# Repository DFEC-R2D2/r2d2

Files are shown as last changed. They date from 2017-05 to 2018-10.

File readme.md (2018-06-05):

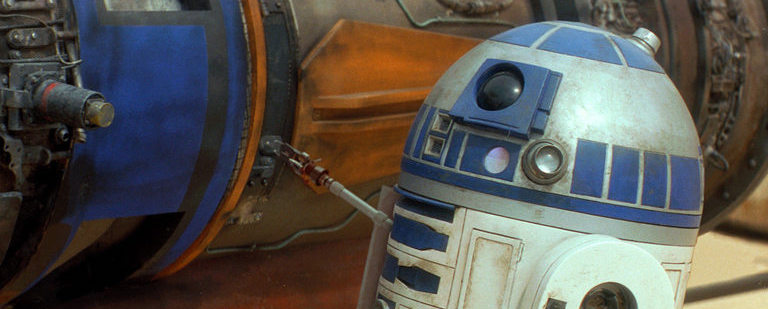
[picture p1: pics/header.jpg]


# R2-D2 Senior Design Project

This repo documents the progress of the R2-D2 design for the 2017-2018 class year. R2-D2's purpose, once
it is delivered, is to:

- Serve as an example of multi-disciplinary engineering
- Support internal events like: Major's Night, DF events, and DFEC events
- Support external events like: STEM outreach and recruiting events.

# Team

- C1C Anthony Talosaga: power system and software
- C1C Hwi Tae Kim: software
- C1C Brayden Thomas: mechanical design and overall build
- C1C Mario Bracamonte: mechanical design and electrical PCD design/construction

# Architecture

## Power

The power system is modeled around a common 12V system. Relays are used to route power for emergency stop, charging, or other reasons. The 12V is split into 5V and 3.3V using voltage regulators to power the raspberry pi, Arduino, pololu motor driver, LED matrix, servos, fan, and the sabertooth motor driver.

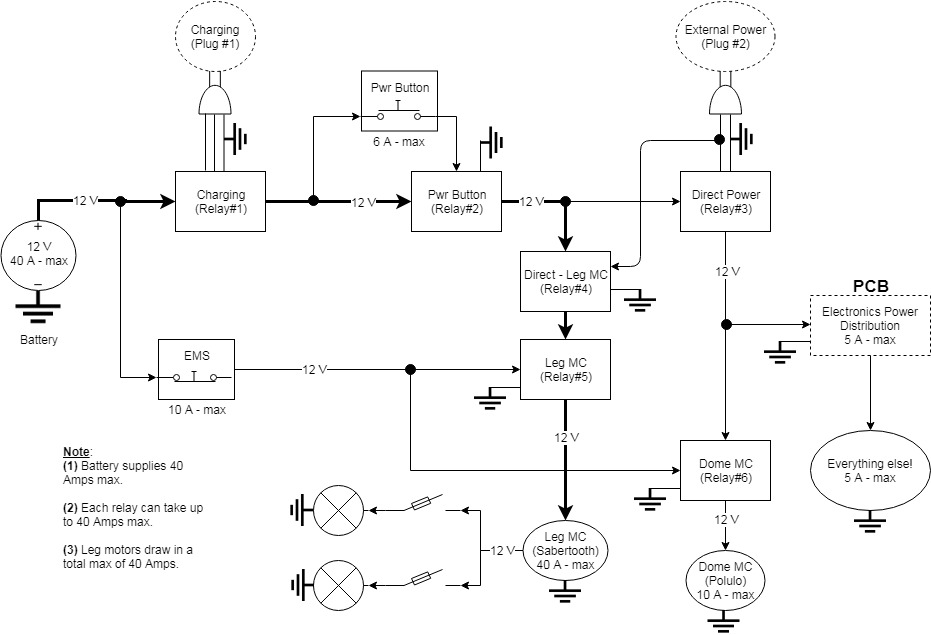
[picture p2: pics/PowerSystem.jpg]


The type of battery that we used for R2D2 is the Motorcycle Battery called Battery Tender Lithium Battery from Deltran. This battery is made from Lithium Iron Phosphate and supplies 12V with 26-35 Amps of power. This allows us to power all the components in R2D2 as well as providing power to the motors, which take up majority of the current.

## Data

The system data shows the wiring between the pi and all of the sensors and effectors. Most of the communications operates at 3.3v, however, there is a USB serial that operates at 5v (5V TTL). The pi uses all of the buses available to it: I2C at 100 Hz, SPI, and USB. The PWM to drive the servos is off loaded to a hardware servo controller board. Similarly, the PWM which drives the motors is offloaded to 2 different motor controllers (Sabertooth and SMC).

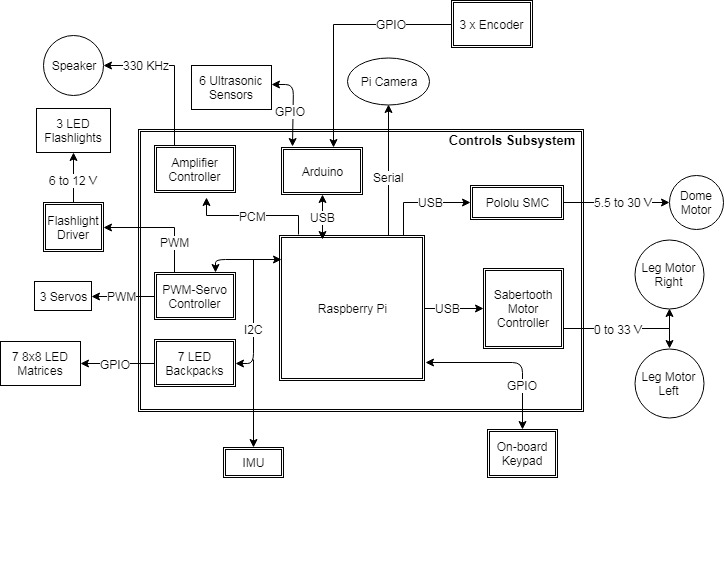
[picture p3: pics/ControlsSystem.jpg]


## Software Operating Modes

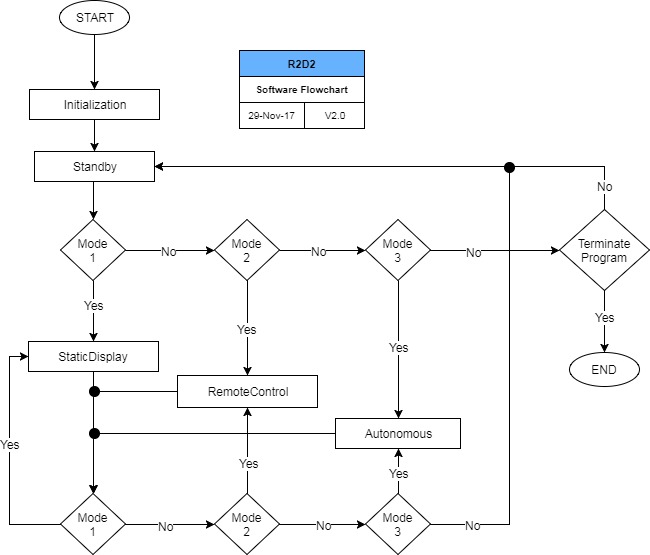
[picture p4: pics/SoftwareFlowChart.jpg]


The system shall follow the transition diagram shown above with the following definitions:

- **Off:** The off mode of R2D2 is when R2D2 is powered off or without any power source. This means that none of the operations are possible, and R2D2 non-functional.
- **Standby:** The standby mode of R2D2 is when R2D2 is remaining idle. None of the motors or the sensors are working in this mode. The Standby mode operates to allow users the ability to fix problems. It is the default mode upon turning R2D2 on.
- **Remote Controlled:** The remote mode of R2D2 can be controlled through the PS4 controller. The instructions on how to connect the PS4 controller to R2D2 can be found in the operational manual. All functionalities of R2D2 is present in this mode.
- **Static Display:** The display mode of R2D2 is used to showcase R2D2. This means that R2D2 is not capable of moving, because it is in display mode. The display mode will respond to people that are close to R2D2.

# Software

R2 is written primarily in python. The following libraries were developed for R2-D2:

- [Text-to-Astromech: ttastromech](https://pypi.python.org/pypi/ttastromech)
- [Simple Motor Controler: smc](https://pypi.python.org/pypi/smc)
- [Sabertooth Motor Controller: pysabertooth](https://pypi.python.org/pypi/pysabertooth)

The following are used:

- [mote](https://github.com/MomsFriendlyRobotCompany/mote)
- [fake_rpi](https://pypi.python.org/pypi/fake-rpi)
- [opencvutils](https://pypi.python.org/pypi/opencvutils)
- [nxp_imu](https://pypi.python.org/pypi/nxp-imu)

Folder structure

```bash
r2d2
|- final_design
   |- arduino
   |- mechanical
   |- node
   |   |-nodejs
   |     |- scripts
   |     |- movies
   |     |- pics
   |- python
      |- clips
      |- library
      |- states
```

- `arduino`: contains the Arduino code. The Arduino talks to the ultrasound sensors and measures the battery voltage
- `mechanical`: containes STL files of parts designed for R2
- `node`: R2's webpage is programmed using nodejs. The `script` folder contains 2 scripts to: 
    - `build_webpages.sh`: generate the webpage html files from Markdown and installs them in the correct location.
    - `gen_qr_code.py`: generate a QR code to enable people to easily access R2's webpage.
- `python`: this is the main *robot* code for R2. The main program is `run.py`.
    - `clips.json`: is a list of available Star Wars sound clips R2 can play

Currently, the Raspberry Pi 3 image that we created allows R2D2 to automatically run this code when booted on. All the USB devices that are connected to the R2D2 are based on our actual model, and would need to be changed to match the serial information of the new device if you are considering making another R2D2. If needed, the image file can be acquired through the DFEC Department Instructor Major Kevin Walchko.

R2 has 3 primary states:

- **standby():** This function is the standby mode function and the default state of R2. Standby does nothing but *standby* for something to happen. If there is an error during operation, R2 switches from his current operating mode and falls into standby. Since standby does nothing, it is seen as the safest mode.
- **static():** This function is the static mode. Static mode is the display mode and it is designed not to allow the leg motors to move. Infact, the electrical design flips a relay and cuts off leg motor power in this state. Only the dome motor and the servos are allowed to move in this state.
- **remote():** This function is the remote mode function, it receives the `remoteflag`, which is set by the keypad on R2D2. This flag is set when 3 is pressed, and continues to be set until R2D2 is put into another mode. The remote mode ensure that R2D2 has full capabilities, such that the motor control works, and all its functionalities are present. R2D2 will be controlled through the PS4 controller. The instructions for connecting the PS4 controller to R2D2 can be found in the operations manual.

| State | Dome Motor | Leg Motors | Audio | Camera | LEDS/Lights | Servos |
|---|---|---|---|---|---|---|
| Standby | | | X | | X | |  
| Remote  | X | X | X | | X | X | 
| Static  | X | | X | X | X | X | 

Helper functions:

- **reboot():** This function is the reboot function. 
- **shutdown():** This function is the shutdown function. 

R2 has to have some personnality, so he is setup with these *emotions*:

- **happy():** This function does not have any inputs or outputs, as the commands are given from the function. The happy function turns on the green LED on the 8x8 matrix LED pads, and also spins the dome. The top hatch of R2D2 will open in a wave and close in a wave. This can be either called from the keypad button 4, or from the arrow hat on the controller.
- **confused():** This function does not have any inputs or outputs, as the commands are given from the function. The happy function turns on the orange LED on the 8x8 matrix LED pads. This can be either called from the keypad button 5, or from the arrow hat on the controller.
- **angry():** This function does not have any inputs or outputs, as the commands are given from the function. The happy function turns on the red LED on the 8x8 matrix LED pads, and plays the imperial theme sound. Once the theme sound is complete, it opens the top hatch of R2D2 and closes it afterwards. This can be either called from the keypad button 6, or from the arrow hat on the controller.

# Project in Pictures

The development of R2 followed a standard Aerospace process of building/testing a breadboard, brassboard, and final design. These follow the ideas of form, fit, and function.

- **Breadboard**: This was the first incarnation of R2. As seen below, it consisted of HW/SW that allowed the team to design/test the functional aspects of R2. The breadboard contained either the actual HW R2 would use or surrogate hardware that was in some way representative (as best as we knew it at the time of the build) of the final design.
- **Brassboard**: This was the second incarnation of R2. Building upon the breadboard HW/SW, all surrogate items were swapped out for the correct items. For example, the breadboard had 3 small 12V motors which represented the dome and leg motors. Now in the brassboard, these small motors were replaced with the final R2 motors. The brassboard now allowed us to test both function and fit. Fit refers to the interfaces, both HW and SW. 
- **Final Design**: Usually you would go to a prototype in the Aerospace world, but here we went straight to the final design. This final design now allowed us to test HW/SW form, fit, and function.  Form refers to either the physical dimension (e.g., the size of a box) or a SW size/processing standpoint for our storage system/CPU.

## Functional Development: Breadboard

This was R2's electronics on a box. It allowed full software design/testing with similar hardware without worrying about actually having R2's body built. Although this looks nothing like an R2 unit, it allowed the team to develop a decent first version of R2. Basic functionallity was achieved including:

- Face detection using OpenCV and the PiCamera
- PS4 controller integration, with analog sticks driving motors, buttons moving servos and making R2 sounds

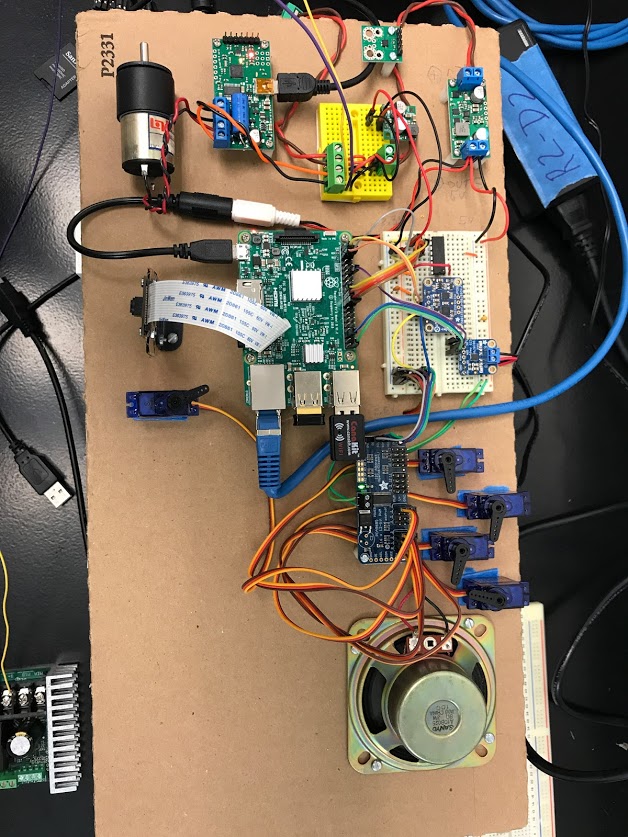
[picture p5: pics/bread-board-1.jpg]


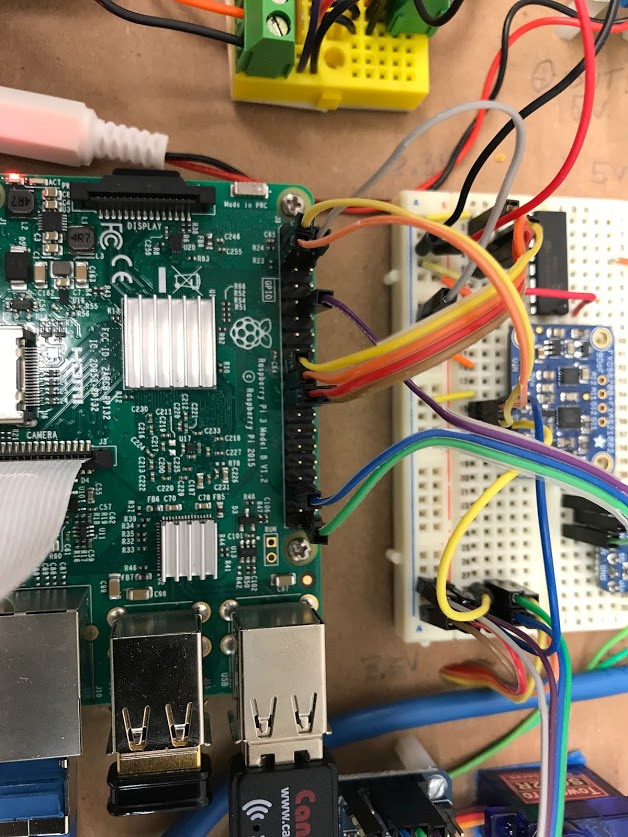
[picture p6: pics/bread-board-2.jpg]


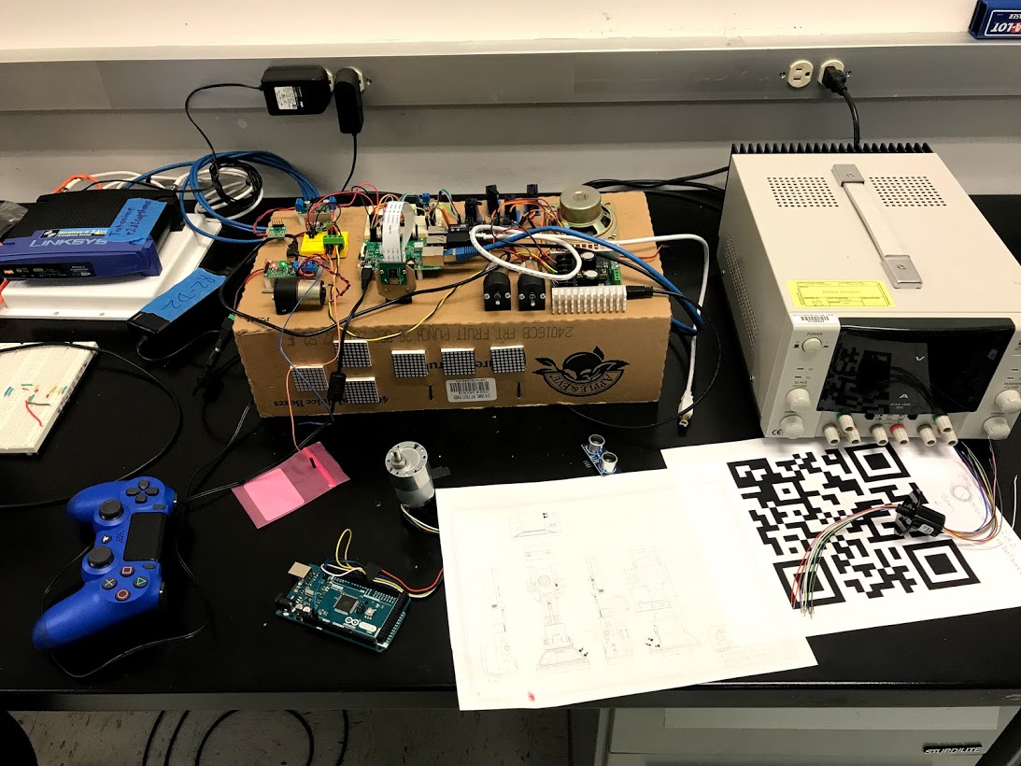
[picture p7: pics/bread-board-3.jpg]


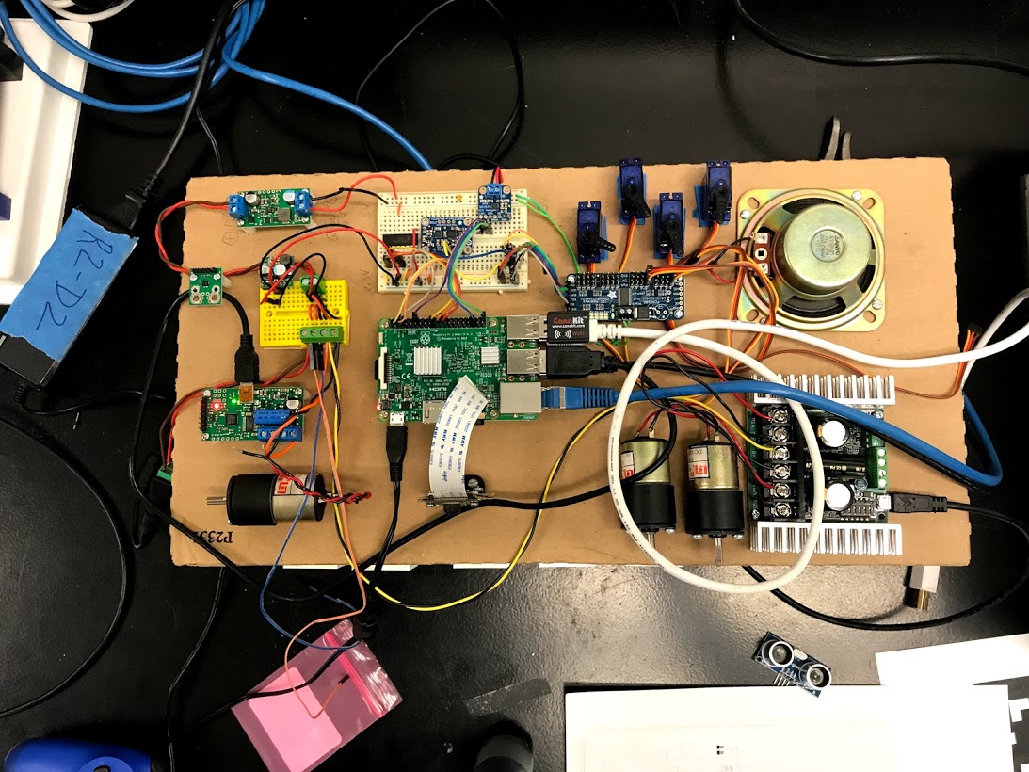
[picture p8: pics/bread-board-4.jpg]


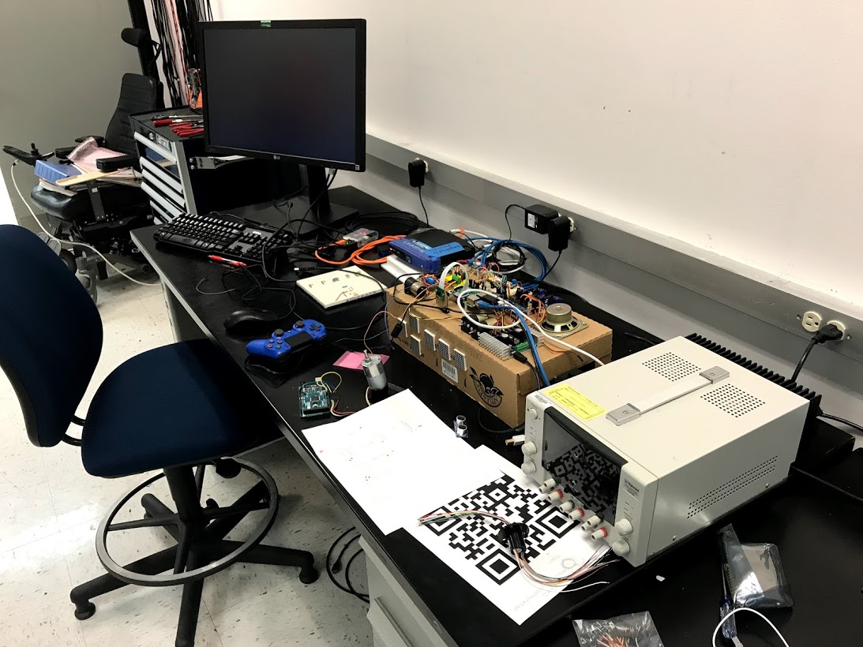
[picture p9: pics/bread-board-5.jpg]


# Fit Development: Brassboard

This was the next level and allowed development/testing against the exact hardware and interfaces in R2. This allowed the team setup the full wiring harness with relays, test out PCBs designed (there were several versions), test out the dome slip ring wiring harness and ensure full HW and SW integration.

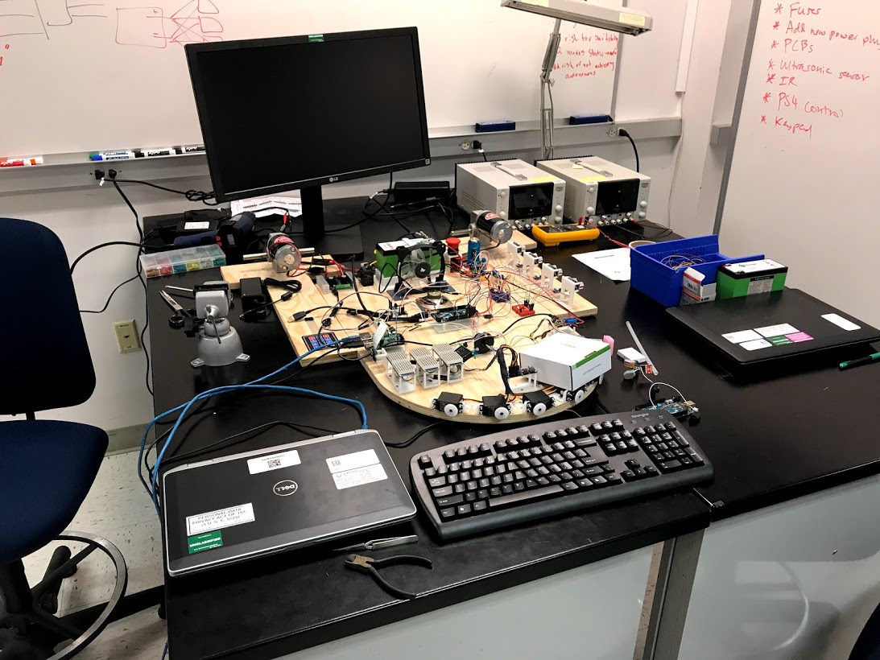
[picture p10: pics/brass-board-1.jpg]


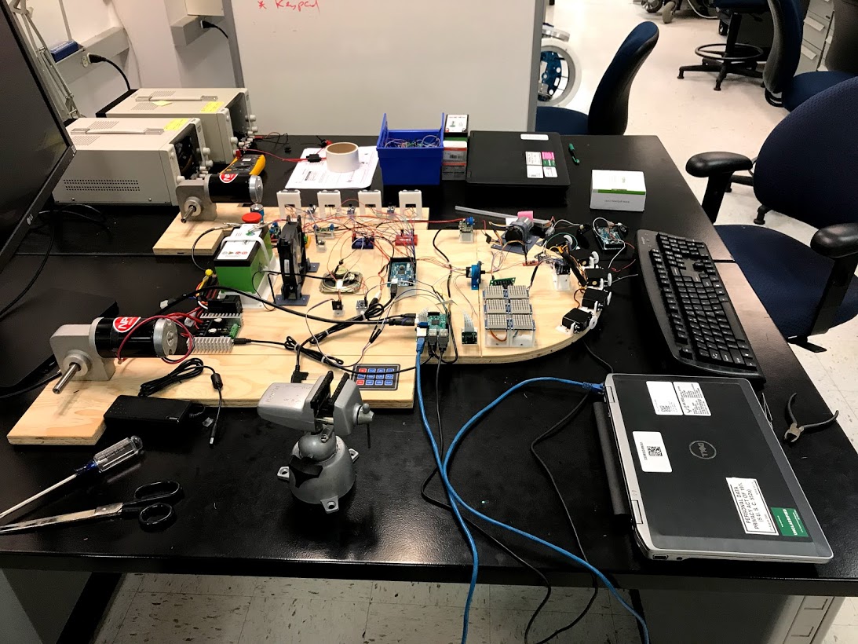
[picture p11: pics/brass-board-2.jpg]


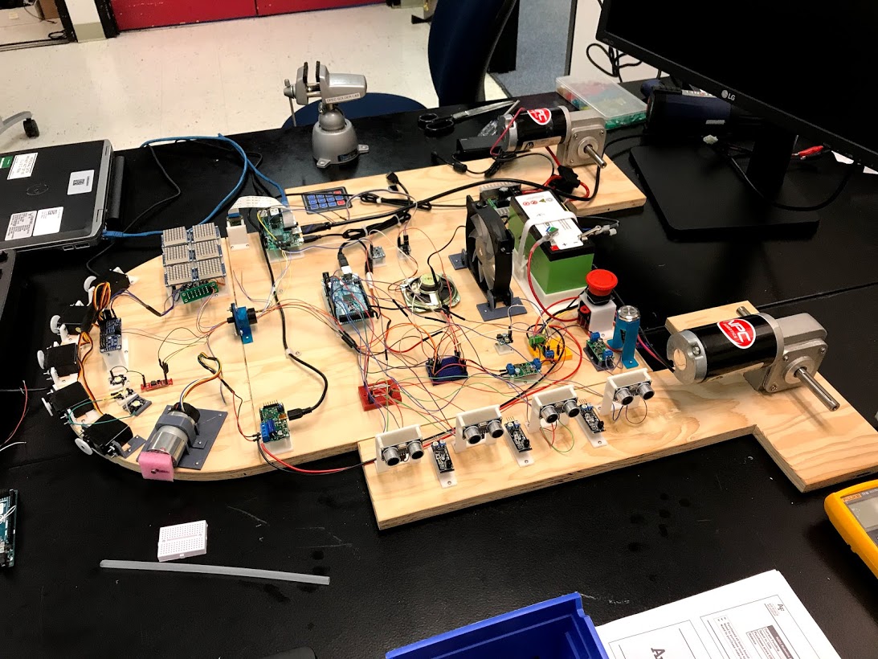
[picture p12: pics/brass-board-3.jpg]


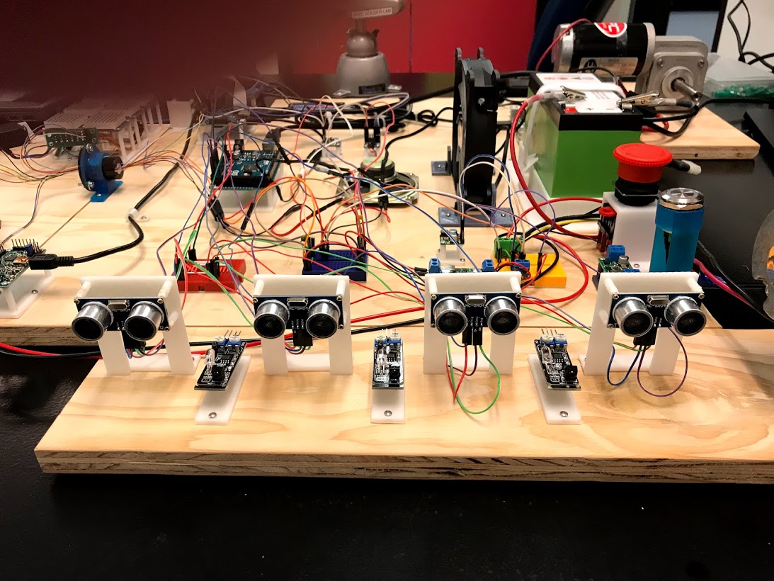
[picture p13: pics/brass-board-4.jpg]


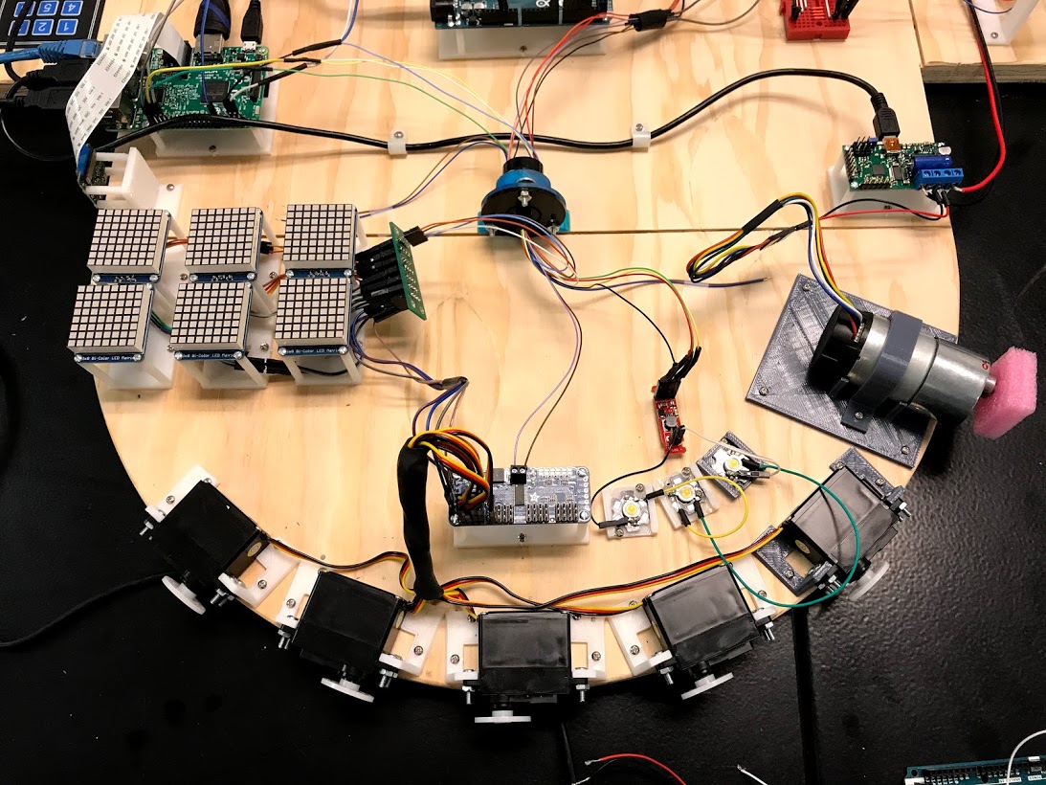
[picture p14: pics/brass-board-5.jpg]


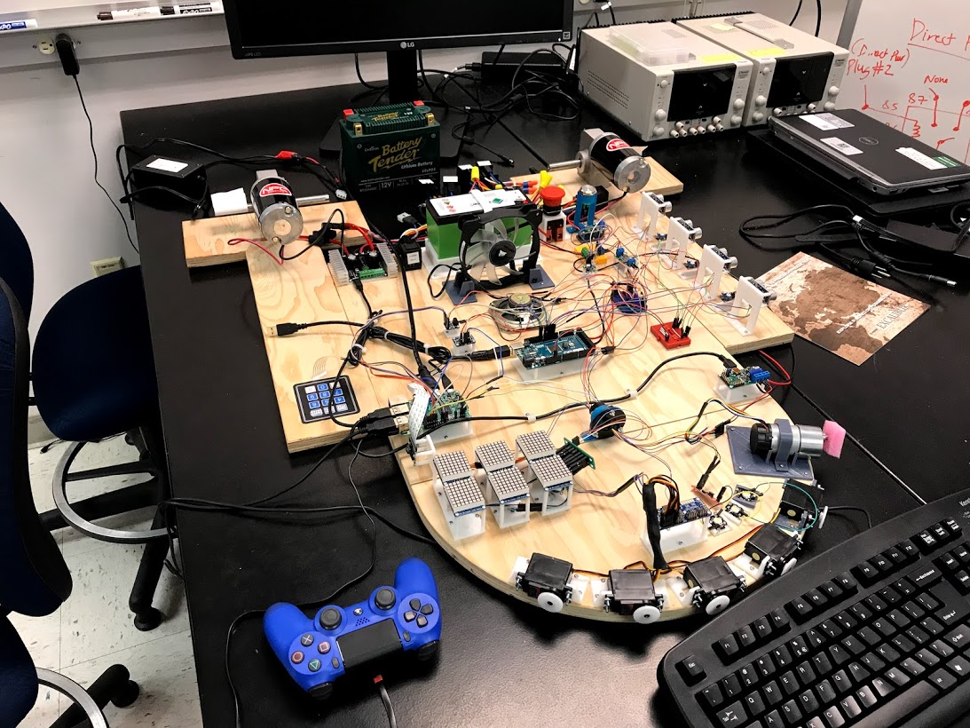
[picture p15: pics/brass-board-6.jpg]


# Final Design and Building

Everything from the brassboard was duplicated and built into the R2. The brassboard was **not** dismantled, but left intact for debugging. The team needed a setup that we could fall back on if HW/SW problems were encountered in the final build. 

Many of the hindges, mounting brackets, etc were designed and 3d printed. The largest design was the 2 rear feet. They were completely designed and 3d printed. Then the motors, wheels, etc were mounted inside and they were painted using Rust-Oleum paint and primer. Unfortunately there were numerous little errors that weren't discovered until everyting was assembled and we had to redesign and rebuild the feet. The feet also took about 2-3 days to print just one ... it was a very slow process.

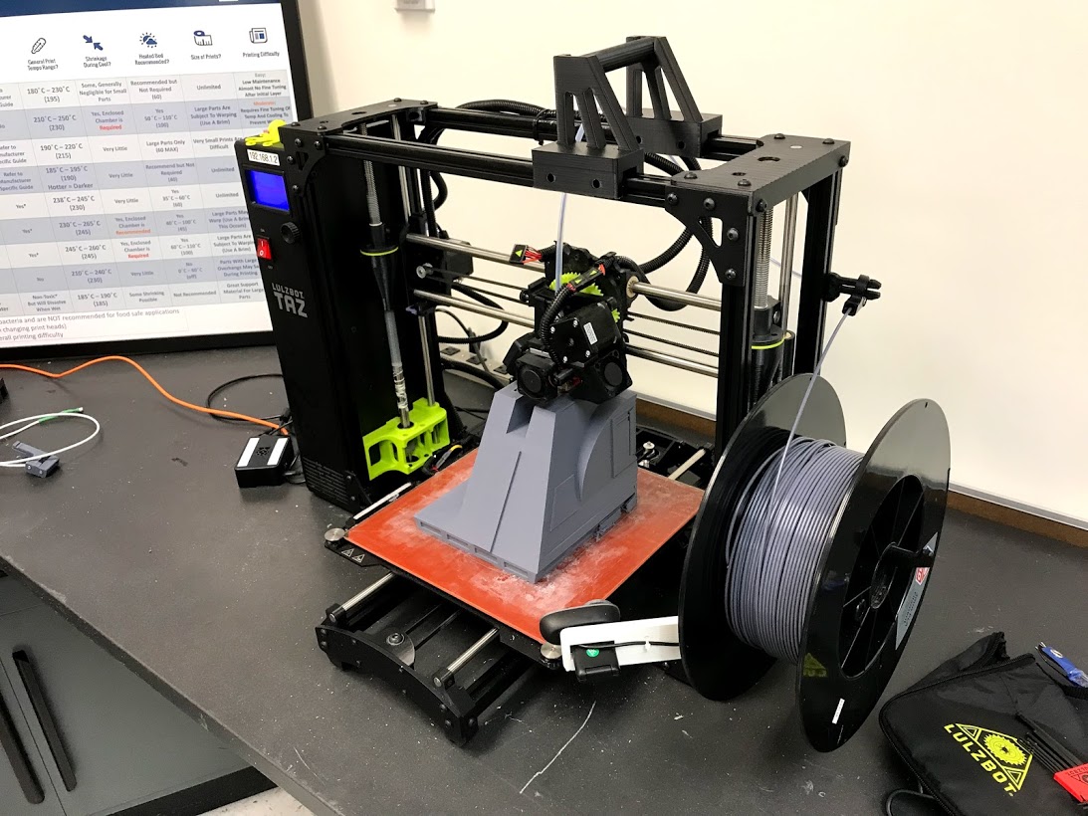
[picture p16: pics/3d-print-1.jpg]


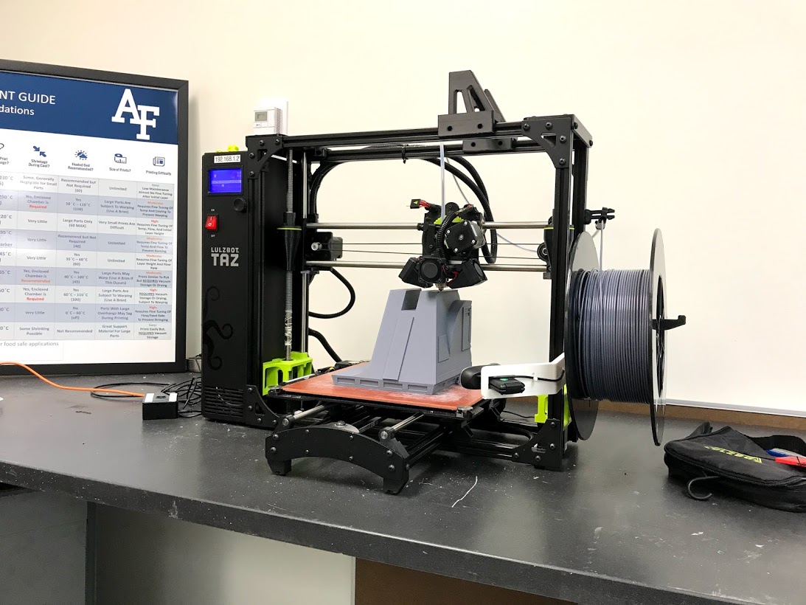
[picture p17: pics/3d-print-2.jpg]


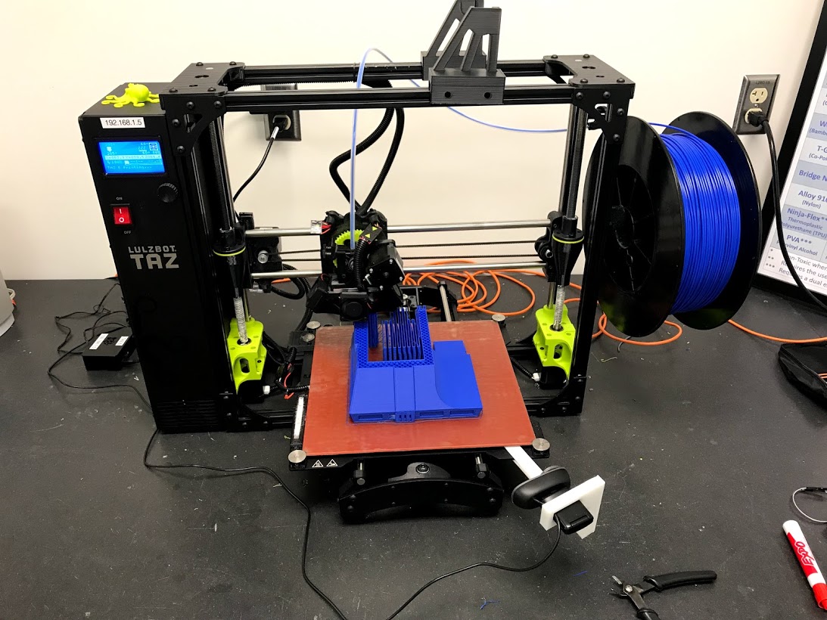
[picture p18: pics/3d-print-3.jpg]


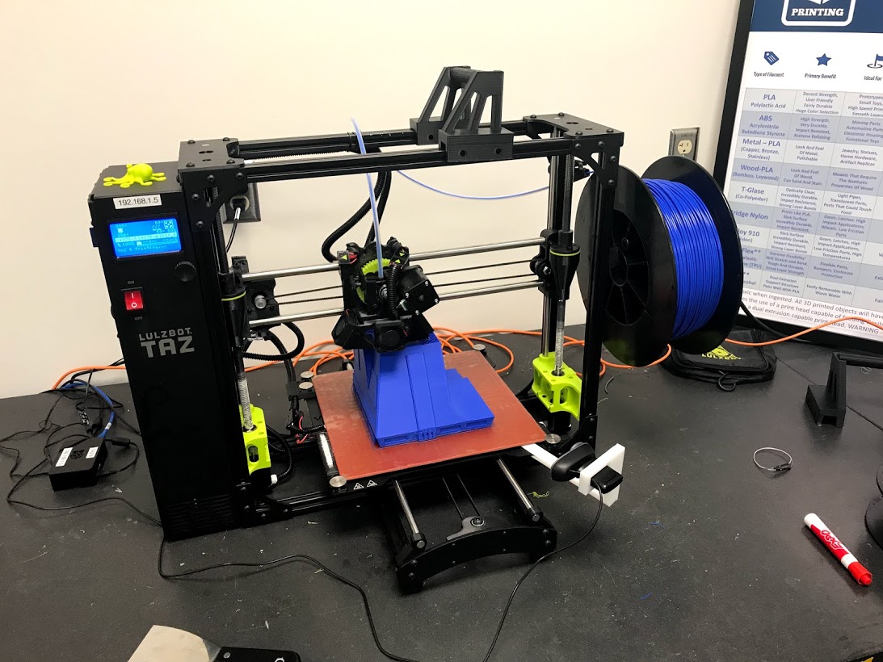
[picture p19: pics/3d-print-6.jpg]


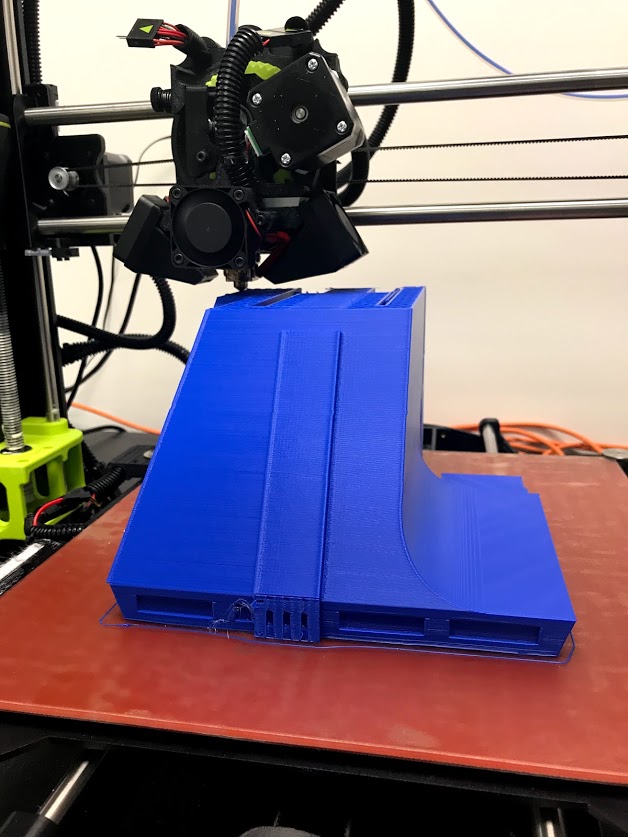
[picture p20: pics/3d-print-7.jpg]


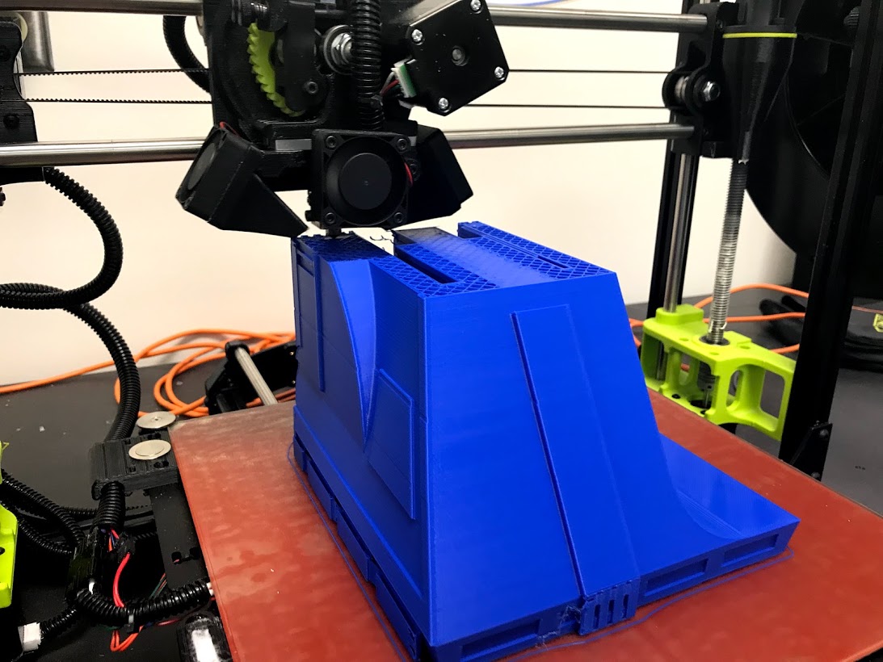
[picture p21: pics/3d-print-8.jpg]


# Integration

## Electronics

All of the electronics in the body were mounted on a clear piece of plexiglass.

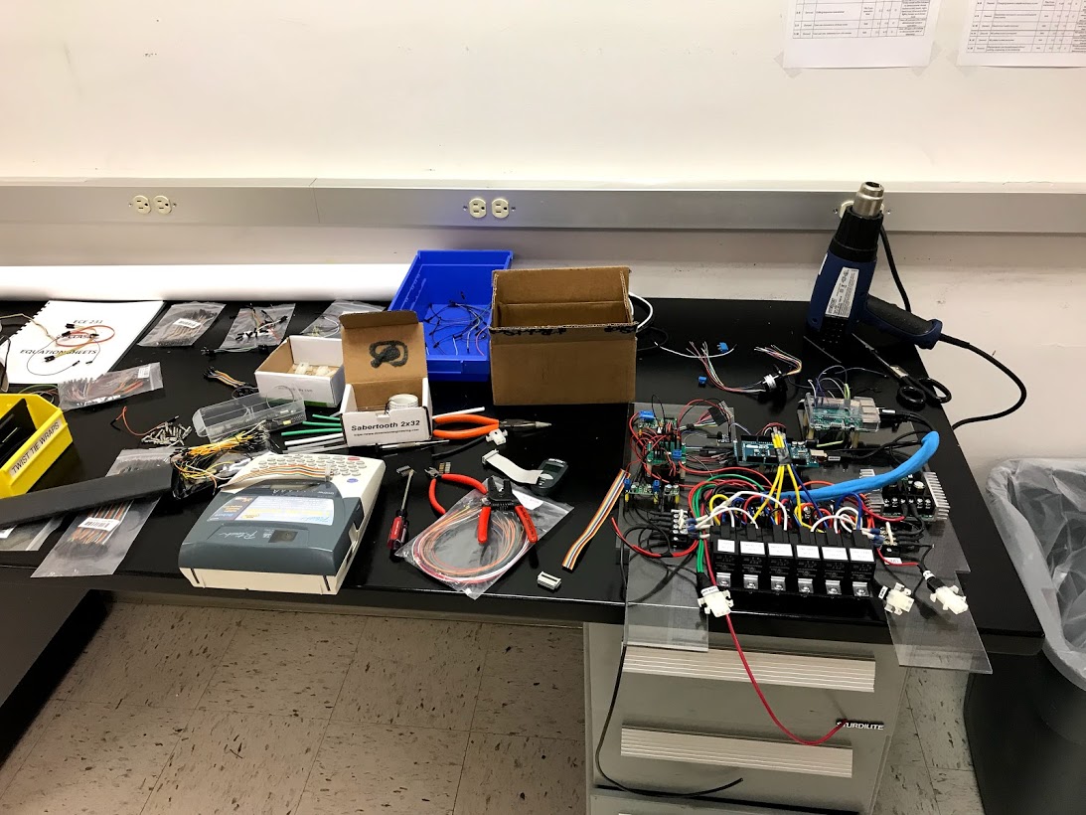
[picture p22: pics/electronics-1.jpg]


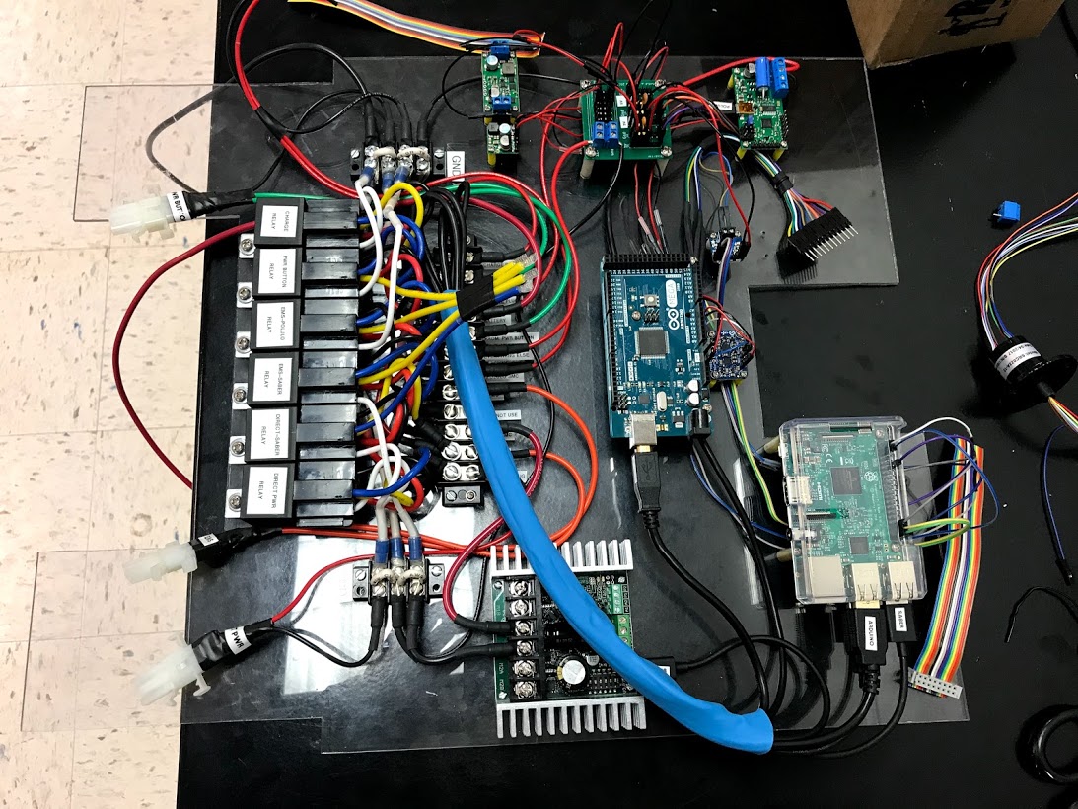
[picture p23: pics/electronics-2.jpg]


## Dome

Mounts for all of the parts were 3d printed and epoxied to the dome. Then the electronics were bolted to the mounts.

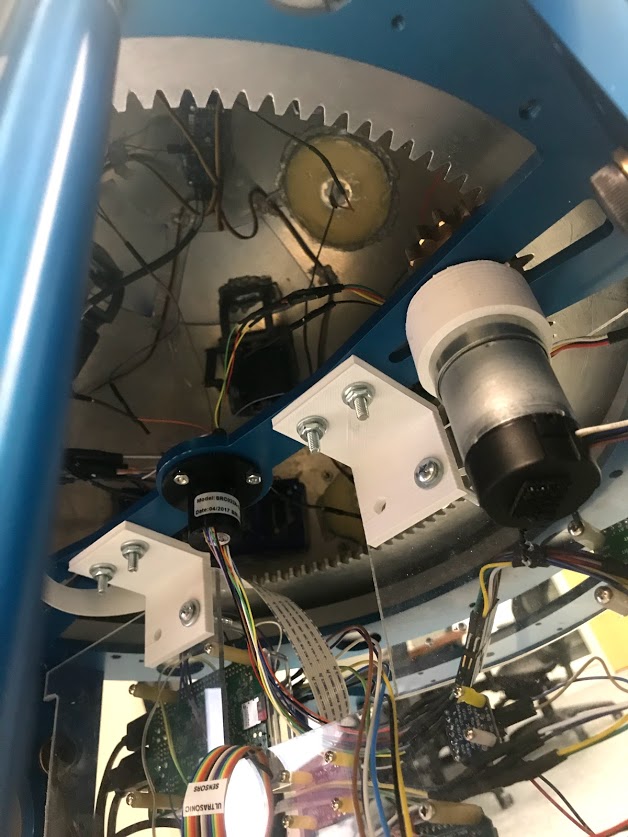
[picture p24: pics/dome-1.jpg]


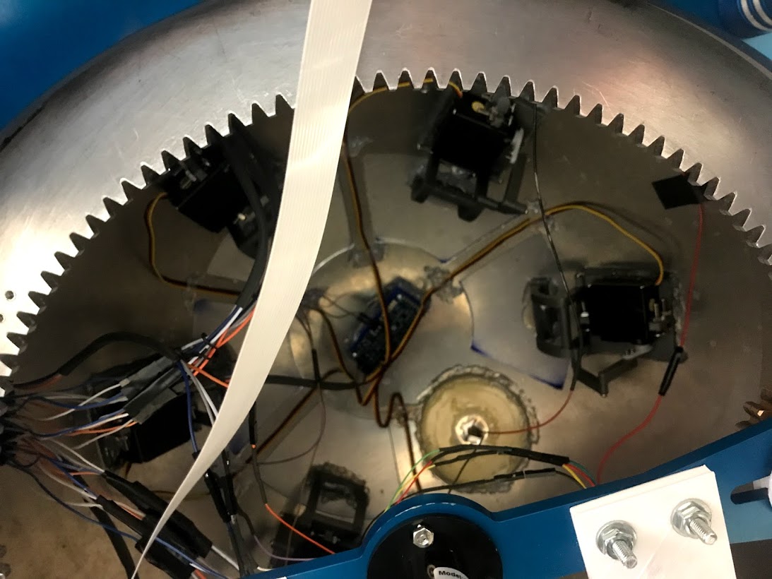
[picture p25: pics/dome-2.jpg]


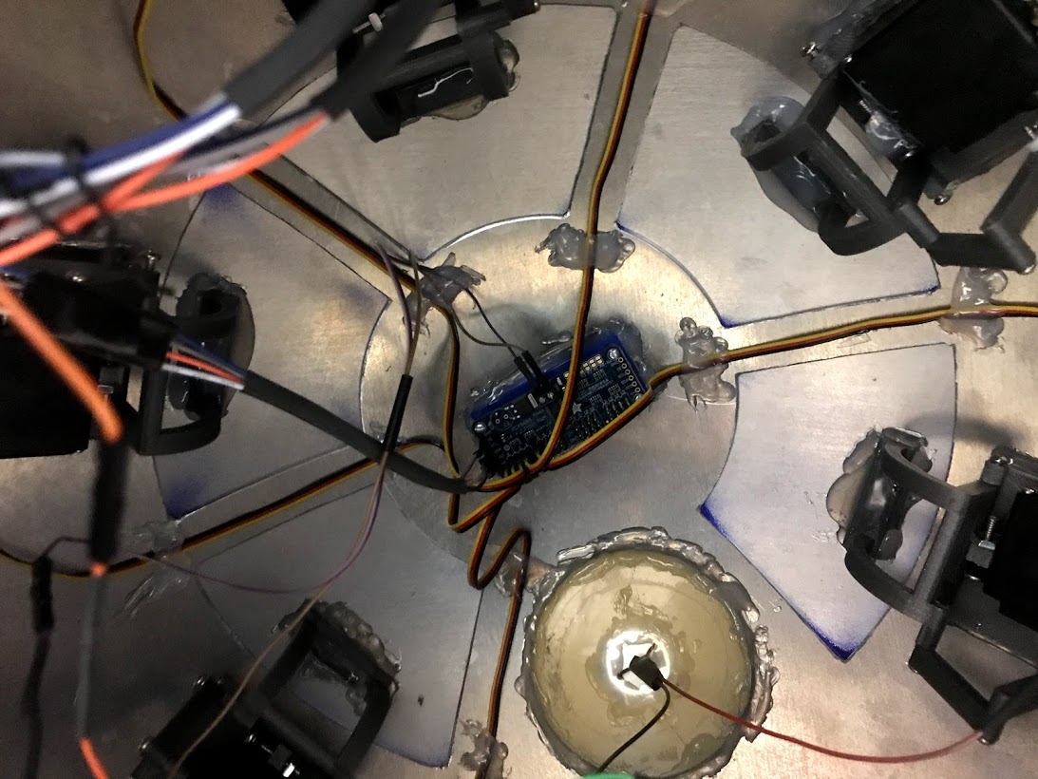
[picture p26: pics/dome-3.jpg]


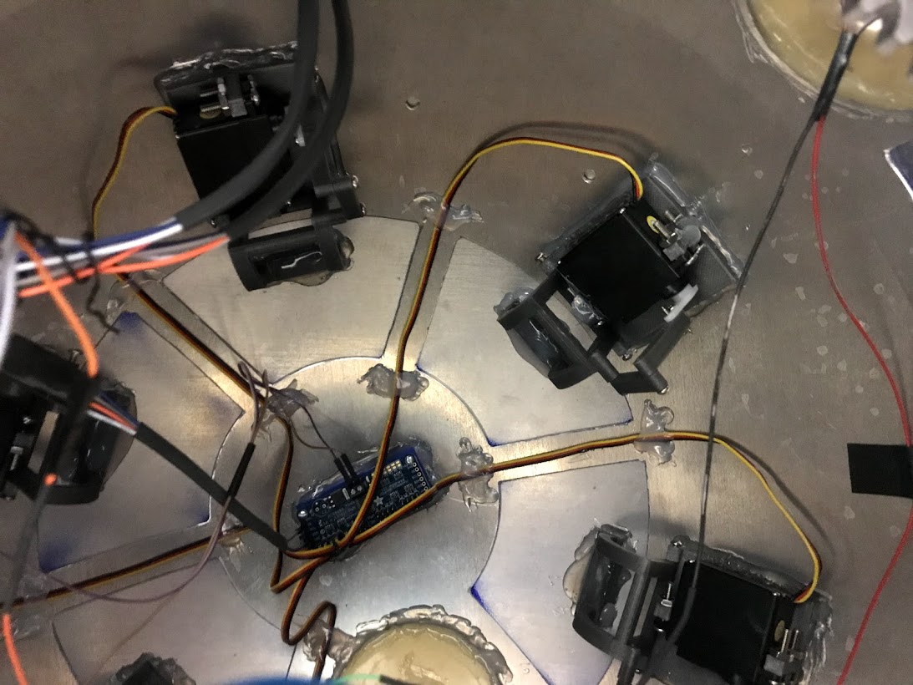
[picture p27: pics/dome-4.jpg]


## Everything Else

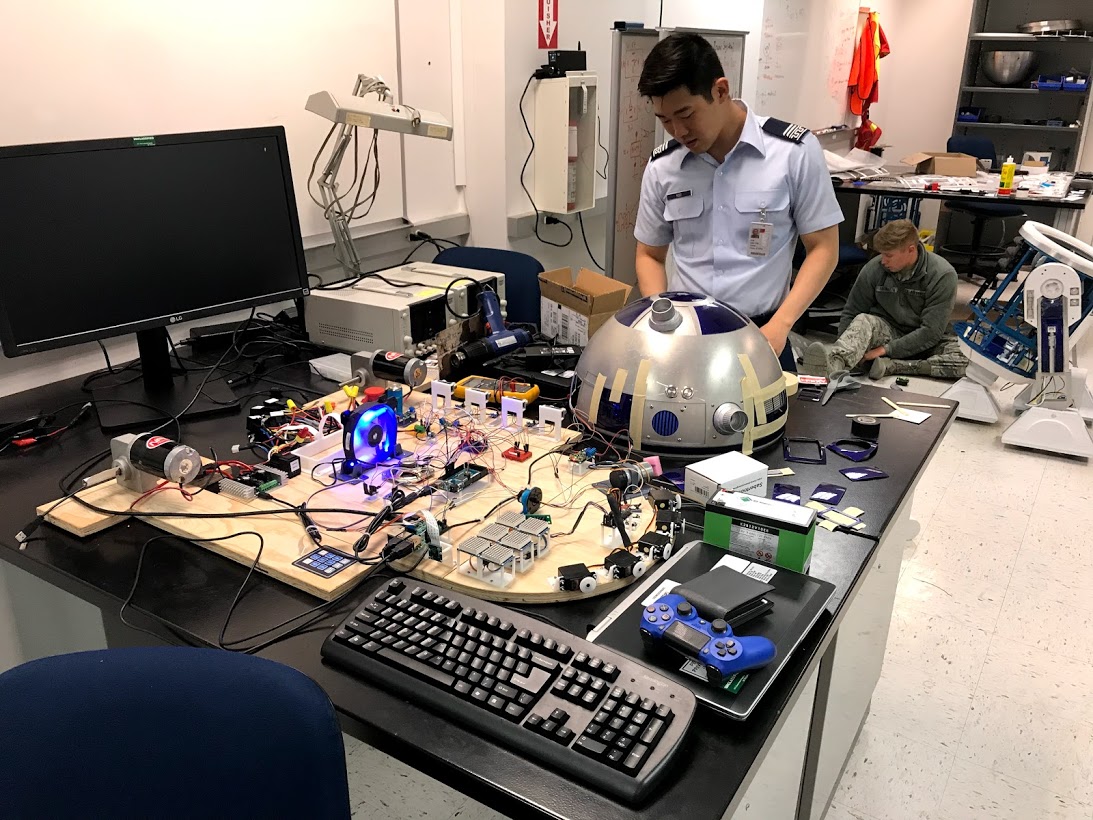
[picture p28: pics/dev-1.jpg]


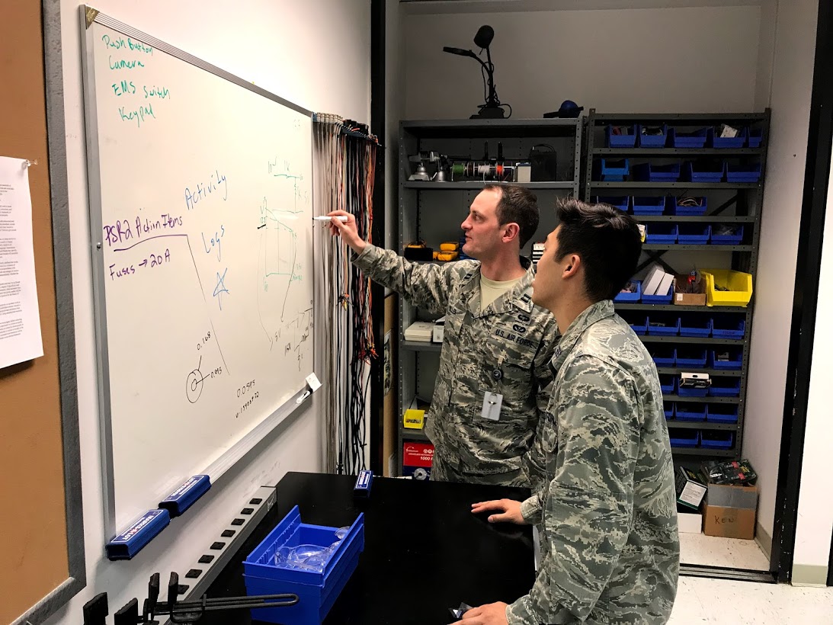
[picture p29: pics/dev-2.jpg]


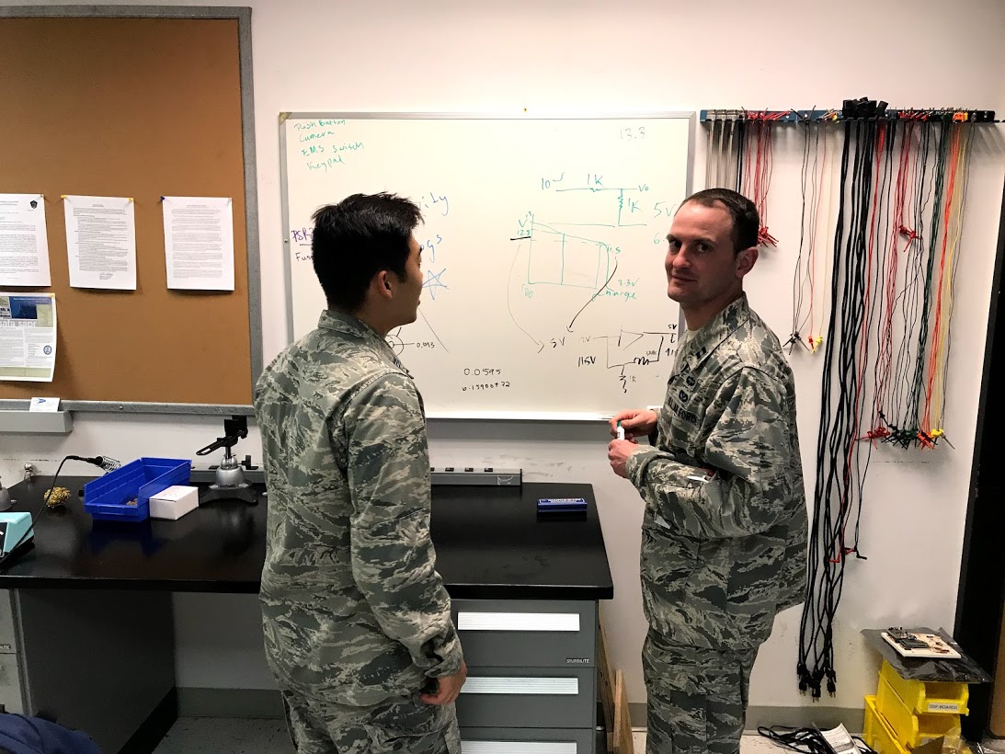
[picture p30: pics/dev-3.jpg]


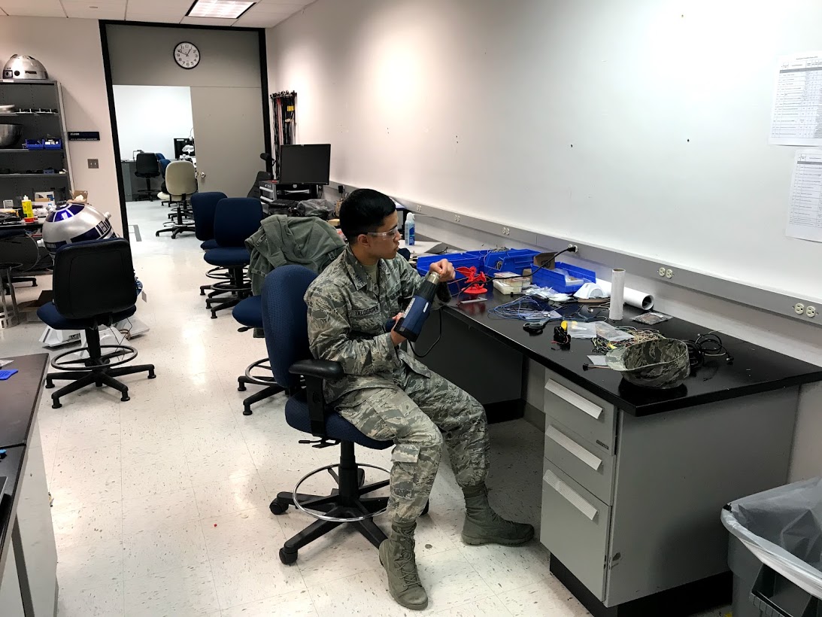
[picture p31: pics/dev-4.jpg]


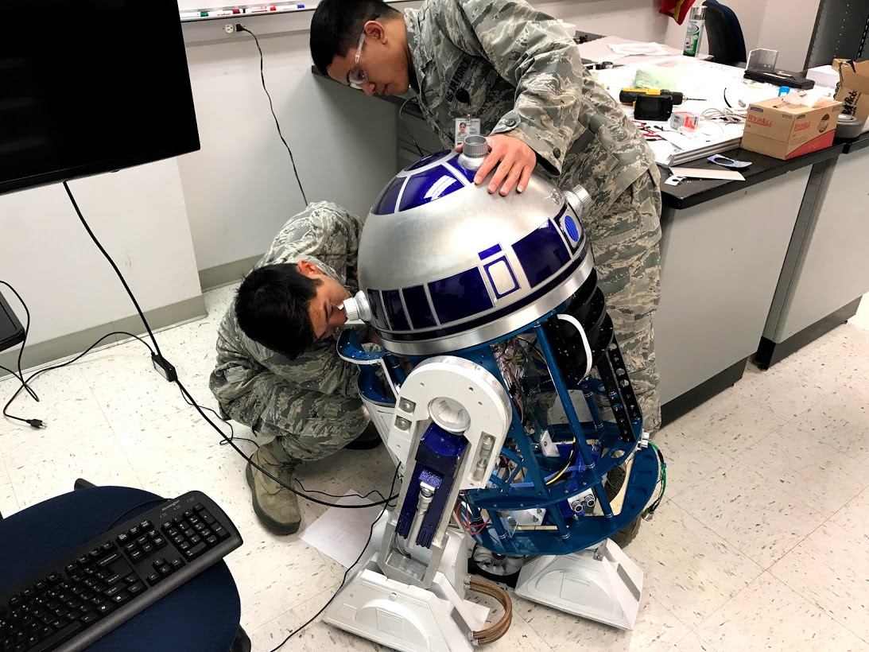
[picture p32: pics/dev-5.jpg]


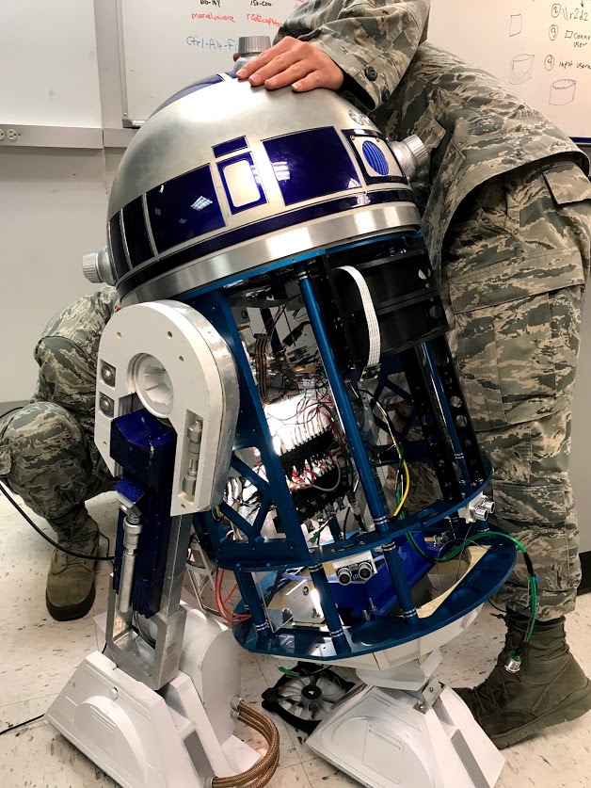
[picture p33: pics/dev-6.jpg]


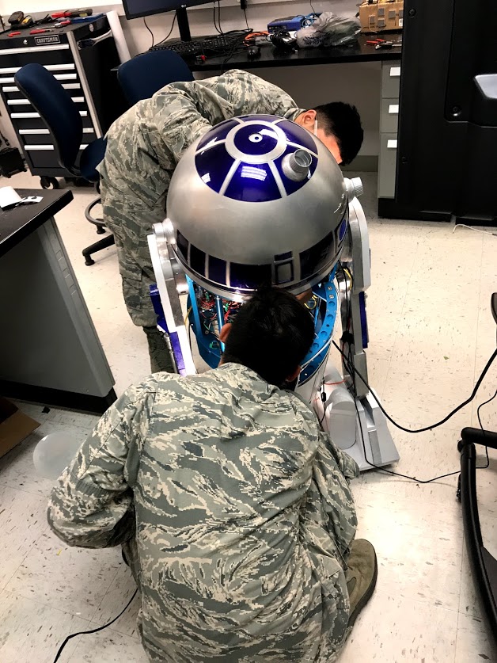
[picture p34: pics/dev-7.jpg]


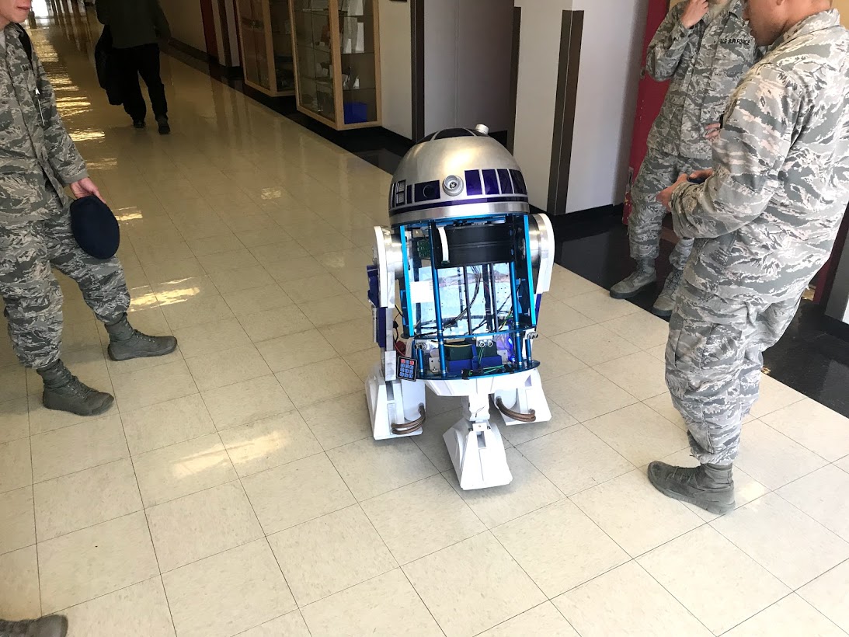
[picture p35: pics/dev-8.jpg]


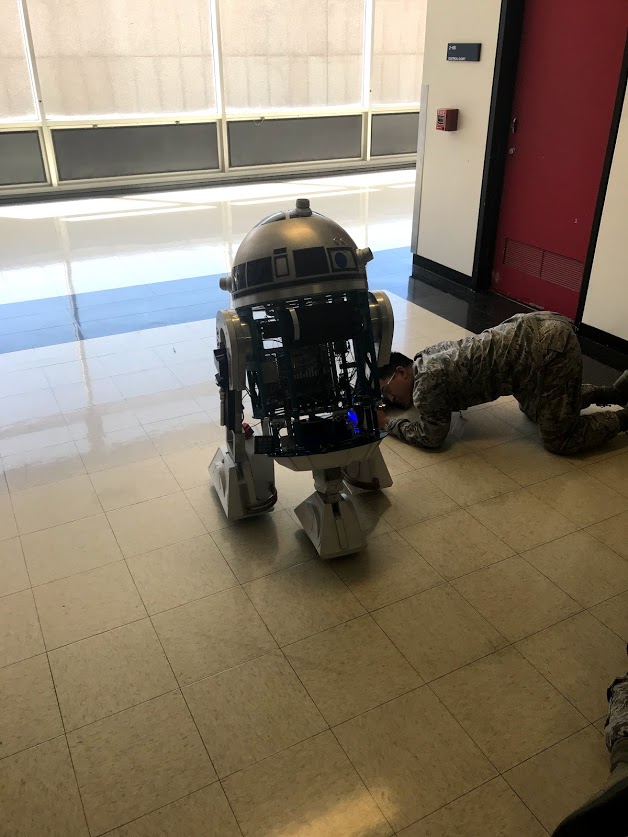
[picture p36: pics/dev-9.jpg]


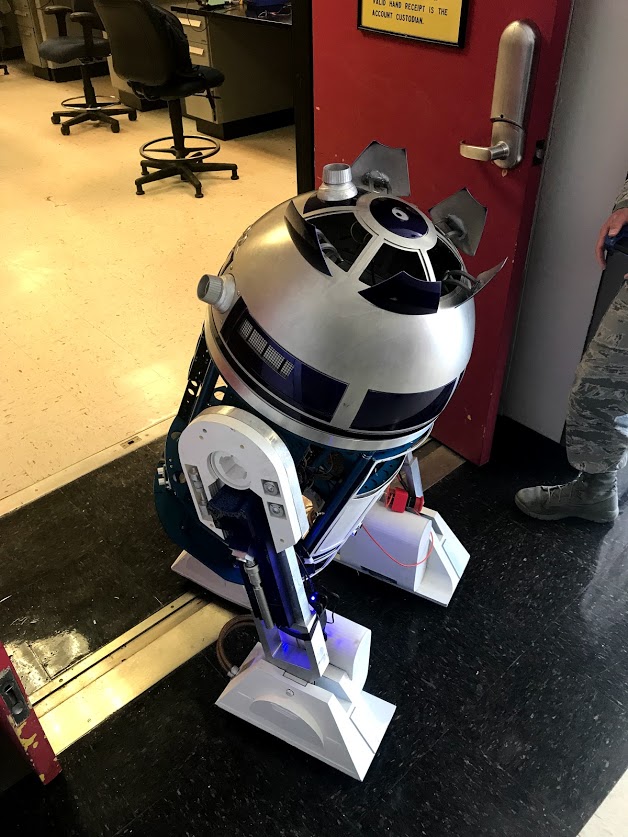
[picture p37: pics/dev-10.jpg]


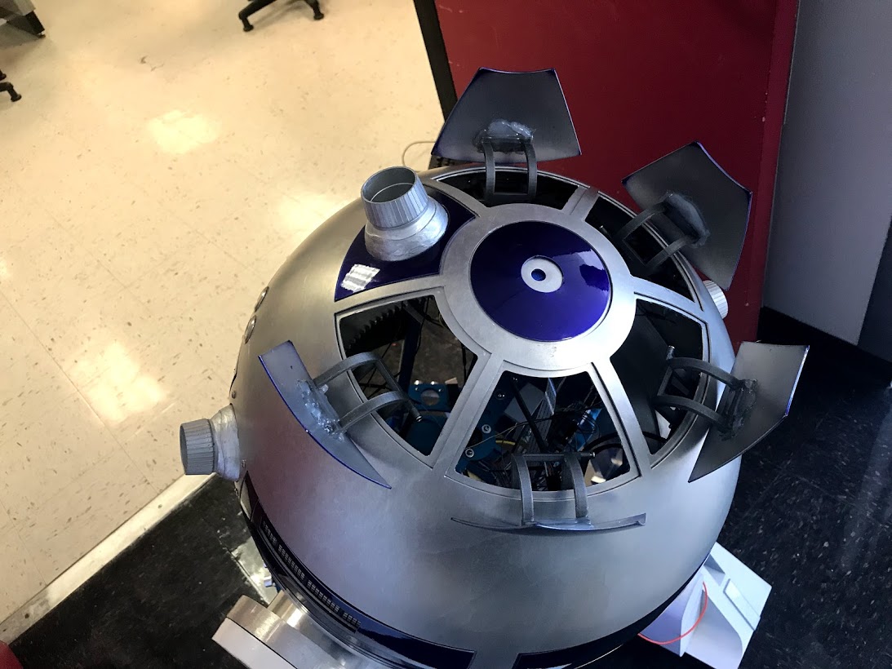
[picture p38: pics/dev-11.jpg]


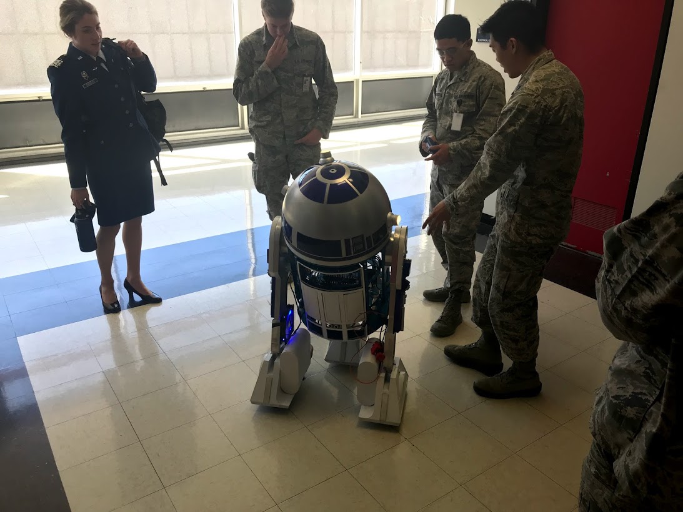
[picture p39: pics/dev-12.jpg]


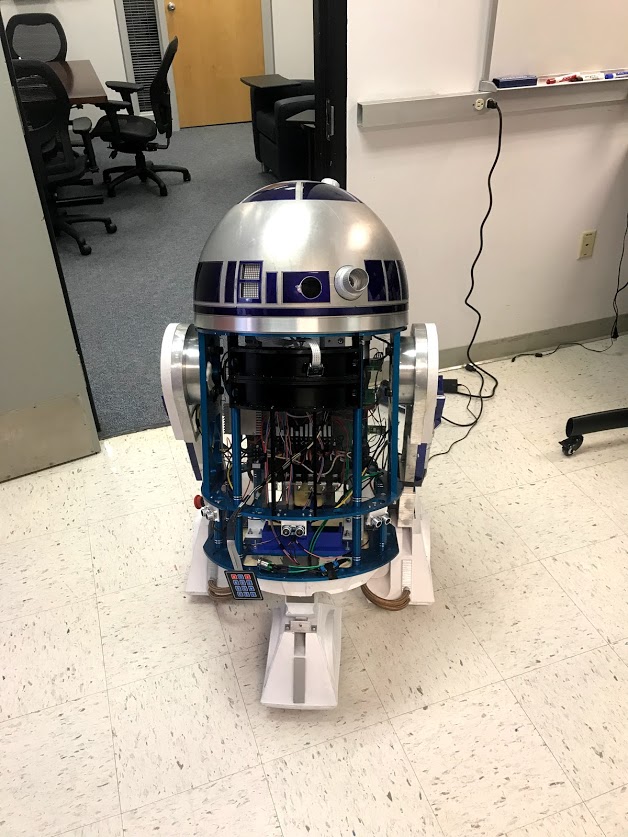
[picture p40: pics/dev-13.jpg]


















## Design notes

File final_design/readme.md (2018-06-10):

# Final Code Design

There are several folders holding the final code:

- `ardunio`: holds the Arduino code for battery monitoring and ultrasound sensors
- `mechanical`: STL files for parts that were designed and 3D printed
- `node`: holds the Node.js web server code and data
- `python`: holds the python and data files that run R2
- `test`: holds a bunch of testing and debugging programs for various parts of R2

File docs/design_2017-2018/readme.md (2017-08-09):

# Design for AY 2017-2018

### Doors

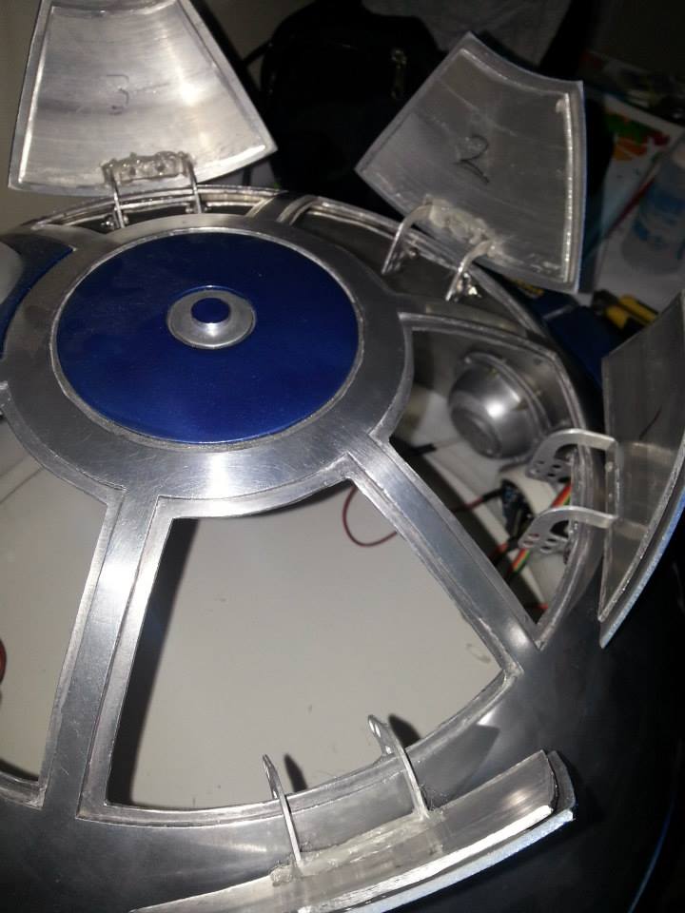
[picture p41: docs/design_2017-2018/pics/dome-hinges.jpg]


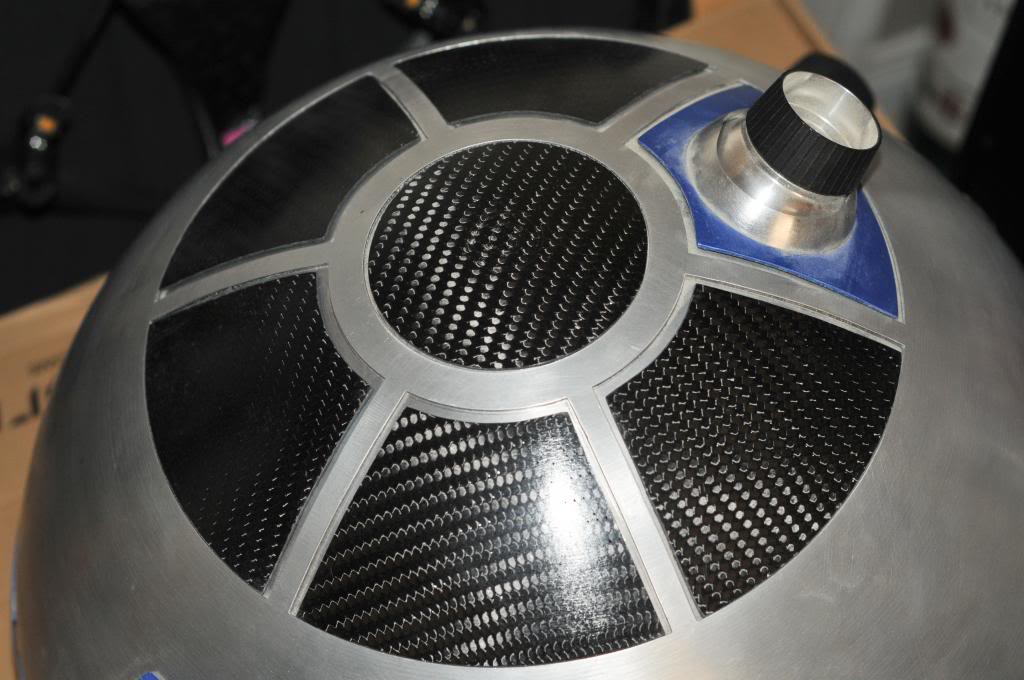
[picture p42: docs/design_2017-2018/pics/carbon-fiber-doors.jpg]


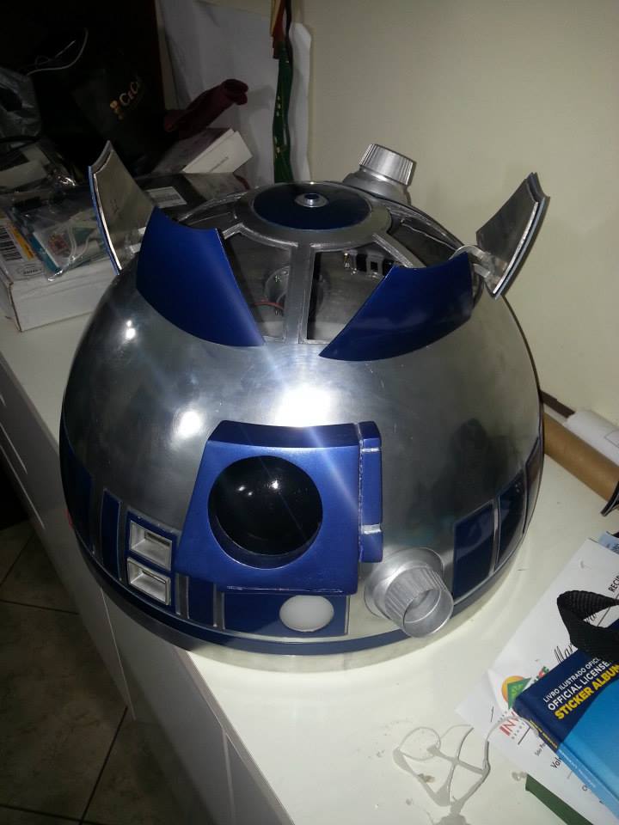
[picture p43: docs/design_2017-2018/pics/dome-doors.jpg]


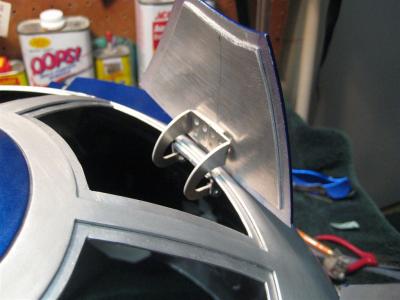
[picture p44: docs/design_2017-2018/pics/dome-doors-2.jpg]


Use servos to open/close doors. If everything is neatly setup inside (with cool
lighting?) it would be an easy method to show off R2's insides.

### Slip Ring

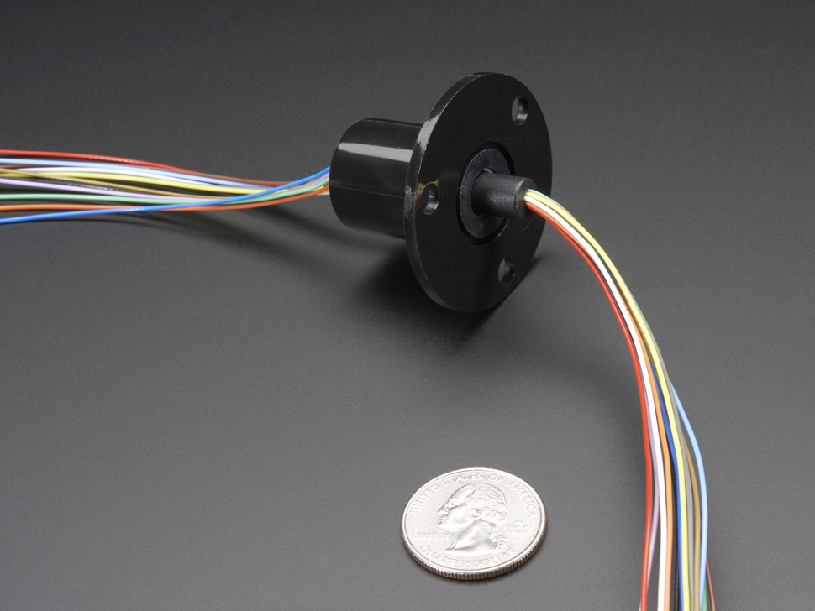
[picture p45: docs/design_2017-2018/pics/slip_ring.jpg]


Previous design didn't use the dome for anything. Apparently doing what everyone else
does and put in a slip ring was beyond their capabilities. We are getting a 22mm 12 wire
(2A per wire) ring from [Adafruit](https://www.adafruit.com/product/1196) which should be
more than enough for power and data. The quetion will be reliability and construction
of said ring.

## Power

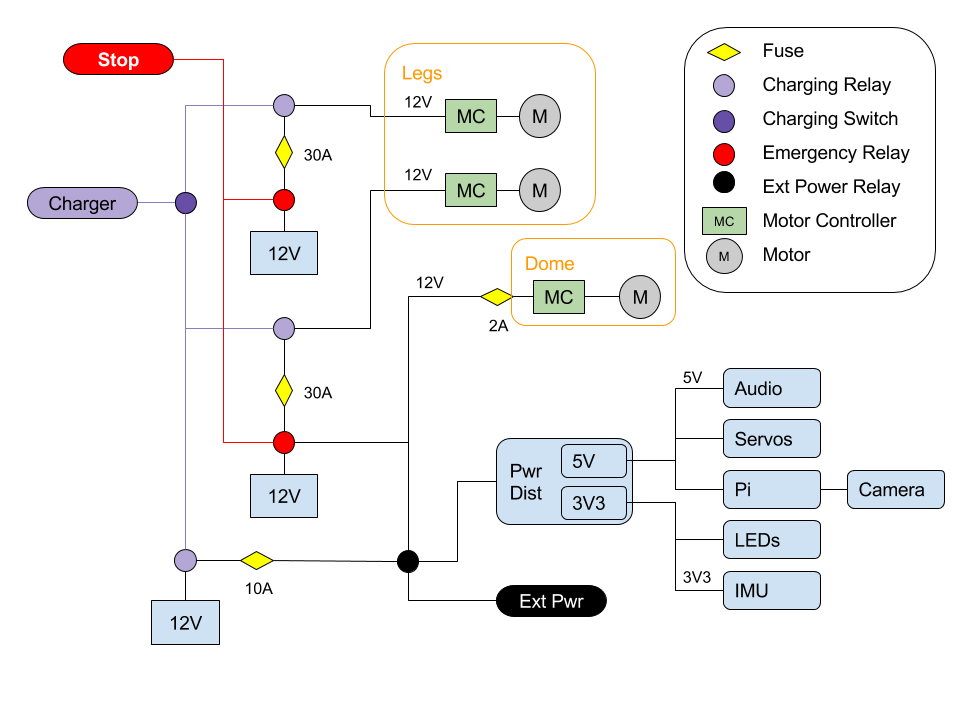
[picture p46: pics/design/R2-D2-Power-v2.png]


Use automotive relays to control power distribution. Basically hook them up
such that when 12V is attached for charging, they automatically disconnect the
batteries from the motors/robot and attach them to the charger.

Since all of the batteries are attached to the charging port, there is a charging
switch (manually operated) that a user must move to determine which battery will
be charged. This could be replaced with a circuit that measured the voltage of
each battery and determined which needed to be charged ... but let's start simple
first.

### Automotive Relay

The relays operate on 12V and can handle between 30A-40A depending on the type. They have 5 inputs:

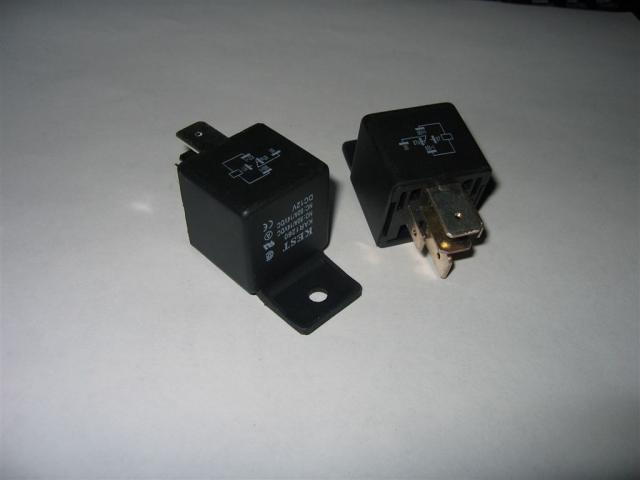
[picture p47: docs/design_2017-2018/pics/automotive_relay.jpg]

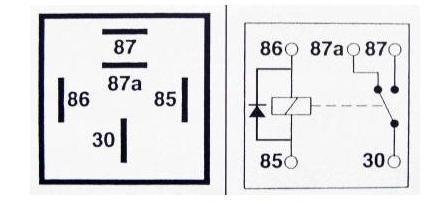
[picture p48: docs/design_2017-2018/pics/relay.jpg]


- **Switch:** When 12V is applied across nins 85 and 86, a magnetic field is created and the relay switches from NC to NO path
- **Normally Closed (NC):** pins 30 and 87a are the default current path
- **Normally Open (NO):** pins 30 and 87 are the alternate current path

Some good references on relays:

- [How automotive relays work](https://www.youtube.com/watch?v=UAeKTlieYhw)
- [Explaination of different relay types](http://www.12voltplanet.co.uk/relay-guide.html)

### Batteries

The last version of R2 had multiple batteries, types, and voltages. This time
R2 will simplify to one type/voltage so we don't have to maintain different charger
and the added complexity that went along with that.

### Protection

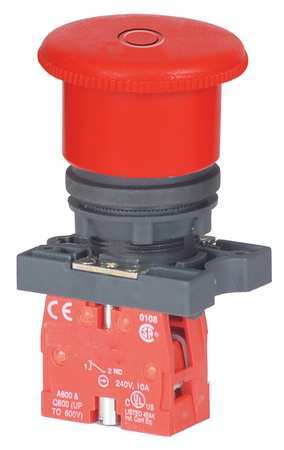
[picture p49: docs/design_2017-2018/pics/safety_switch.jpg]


Add a real emergency kill switch that cuts power to the motors. Prefer not to kill power to
the computer (typically not a good idea), plus, no one can get hurt by a raspberry pi.

The fuses are based on the last design. Not sure how much current is actually needed by the
leg motors nore what the continous discharge rate of the selected batteries are.
All of the fuses will have to be properly sized.

### External Power

It is desired that R2 also serve as a static display. Being able to plug him into the
wall (automatically disable the leg motors so he can't move) and power the electronics
and maybe just the dome/periscope motors. In this configuration, the emergency safety
wouldn't work on the dome/periscope motors (remember the legs *are* disabled), but if
anything goes wrong, just pull the external power. Thinking a 12V 5A wall wart would work.

## Human Machine Interface

### Buttons

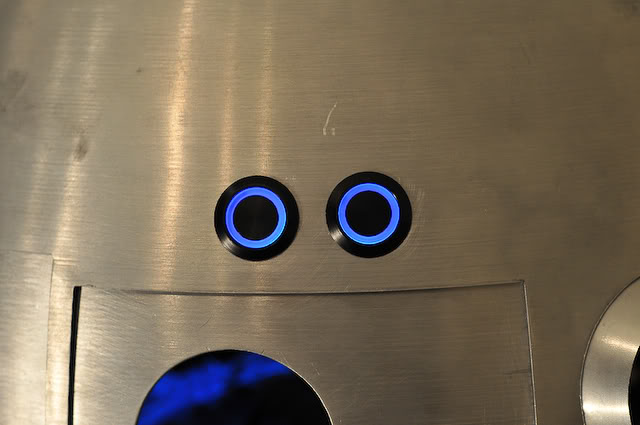
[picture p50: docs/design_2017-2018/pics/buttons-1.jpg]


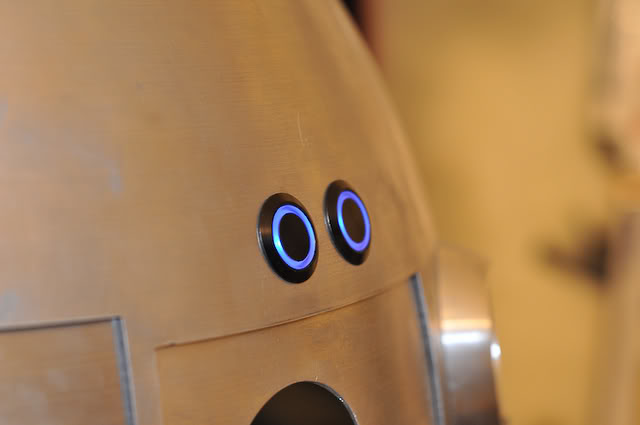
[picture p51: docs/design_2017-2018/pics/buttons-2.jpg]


We could tie these to power up or reset the R2 electronics or cycle through operating modes.

### Displays / Lights

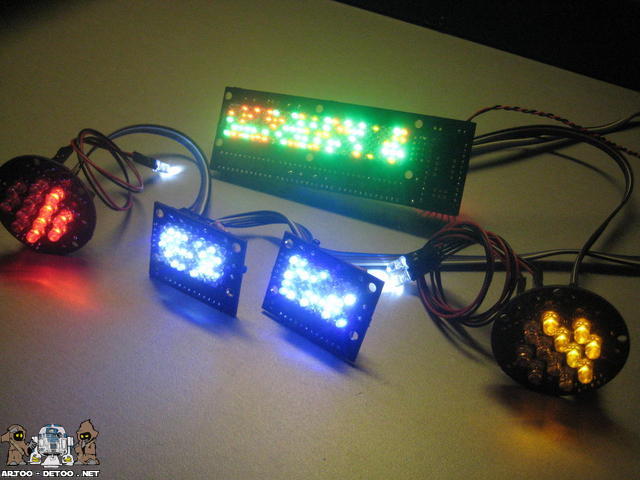
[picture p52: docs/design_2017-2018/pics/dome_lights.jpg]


This would be a great human-machine-interface thing if you could make the lights mean something.
Otherwise, random blinking is fine.

### Web Server

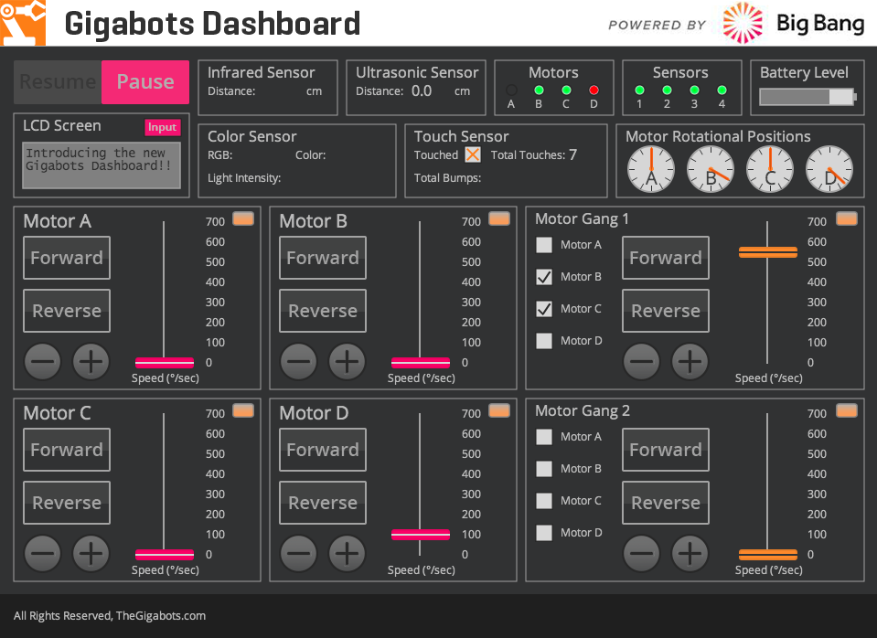
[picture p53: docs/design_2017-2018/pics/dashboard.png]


Not hard, maybe something that displays a bunch of information. Note, the one shown above is not
necessarily what we want, just the first example found on the interweb.

Taking a look at [D3.js](https://github.com/d3/d3/wiki/Gallery) in the basic charts section, we
could:

- donut chart on power system
- line chart on motor currents
- radar chart to display 360 deg sensor info

## Motor Controllers

Initial analysis is [here](motors.ipynb)

## Dome Motor

TBD

# How Ours Should Look

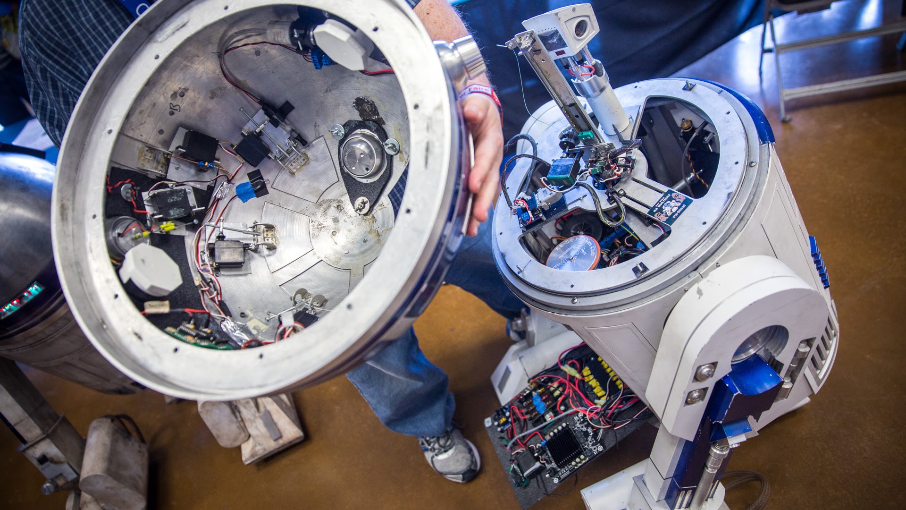
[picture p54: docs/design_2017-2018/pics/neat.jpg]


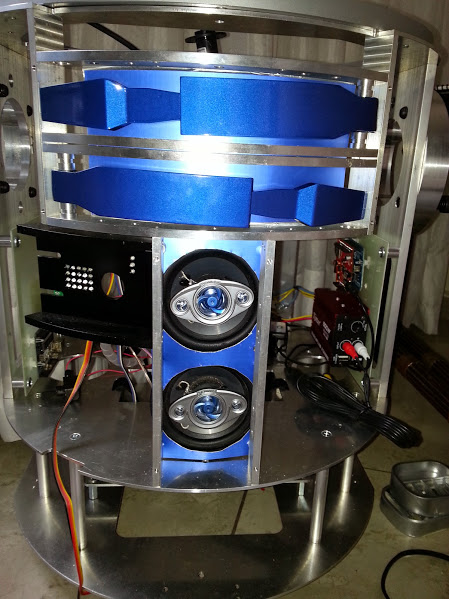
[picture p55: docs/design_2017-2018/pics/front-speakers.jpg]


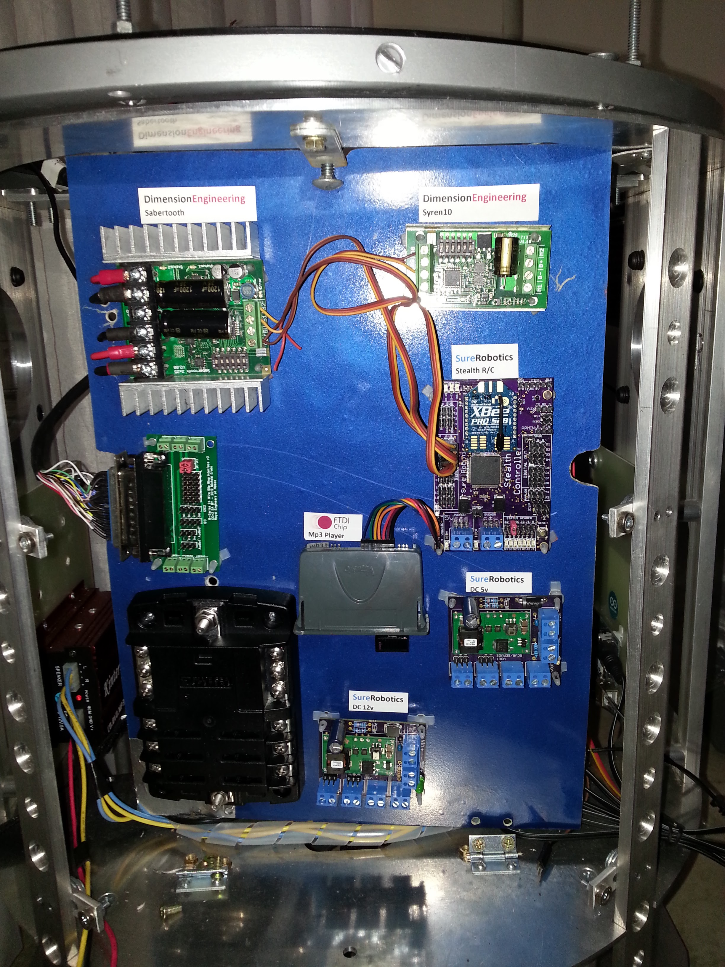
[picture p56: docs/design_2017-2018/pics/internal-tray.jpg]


## Other Layouts

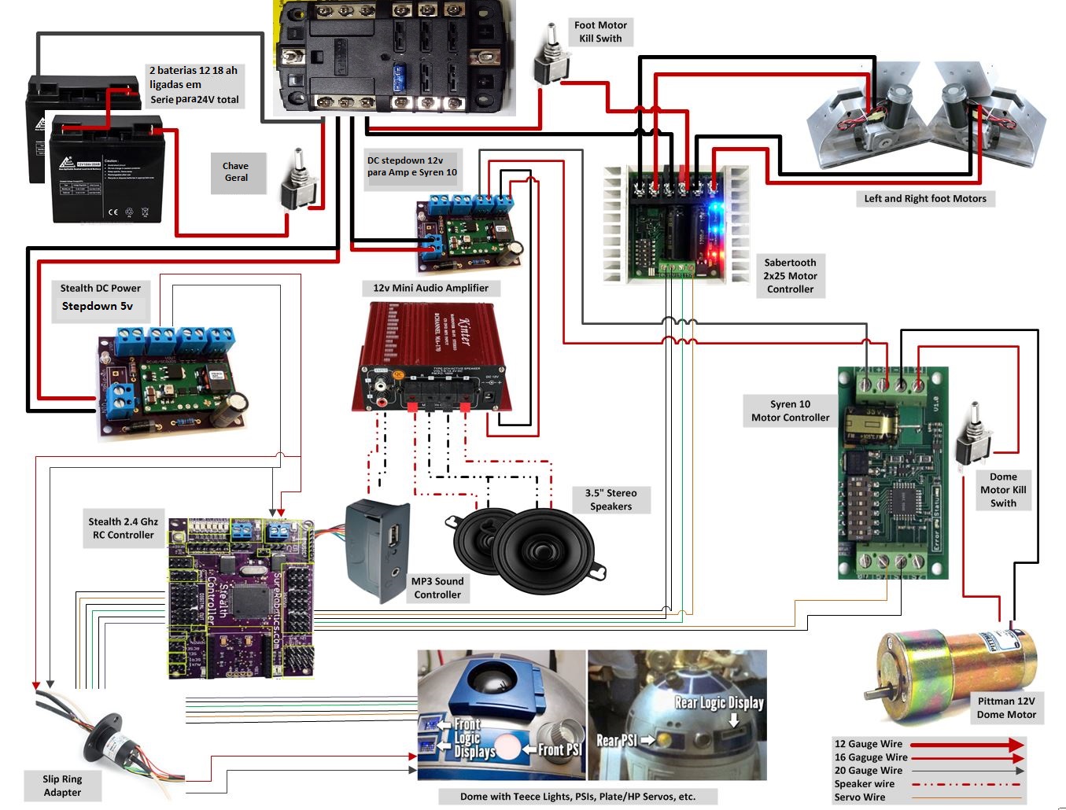
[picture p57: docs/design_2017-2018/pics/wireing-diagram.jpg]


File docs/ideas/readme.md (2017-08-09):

# Ideas - old

## Under the Dome



##### Yes, the Simpson's did it before Stephen King

### Doors









Shouldn't be too hard ... hinges, servos, etc.

### Lights



Would like to do the lights for R2. There are all kinds of kits or do-it-yourself. Leaning
towards simple LED matrices with I2C comm. Would be a great human-machine-interface
thing if you could make the lights mean something. Otherwise, random blinking is fine.

### Slip Ring



Previous design didn't use the dome for anything. Apparently doing what everyone else
does and put in a slip ring was beyond their capabilities. We are getting a 22mm 12 wire
(2A per wire) ring from [Adafruit](https://www.adafruit.com/product/1196) which should be
more than enough for power and data. The question will be reliability and construction
of said ring.

## Data

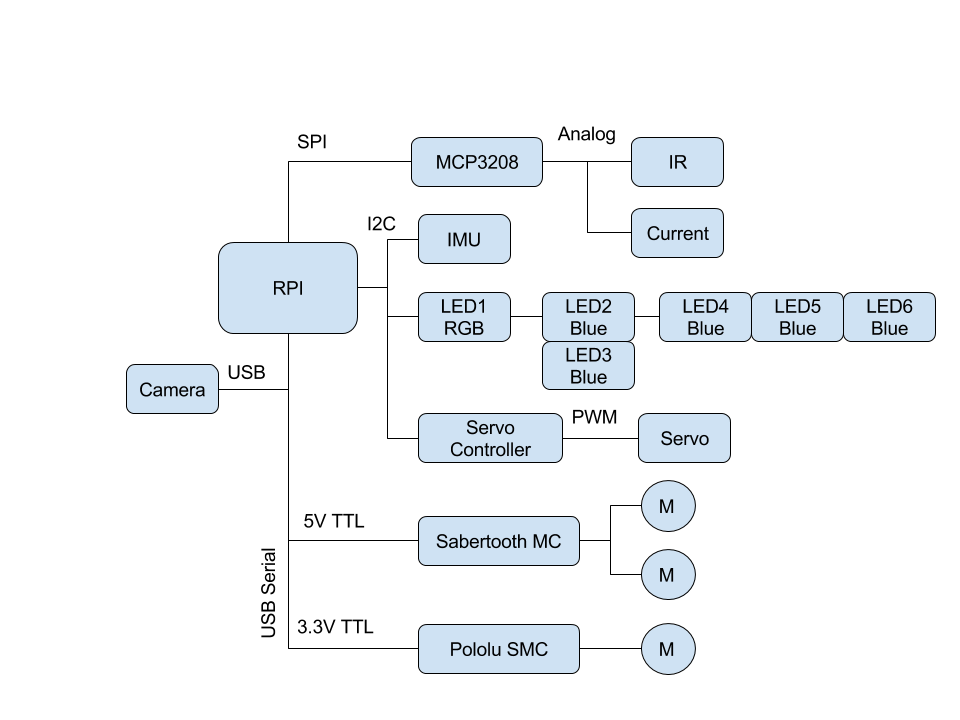
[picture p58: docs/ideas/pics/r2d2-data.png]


## Power

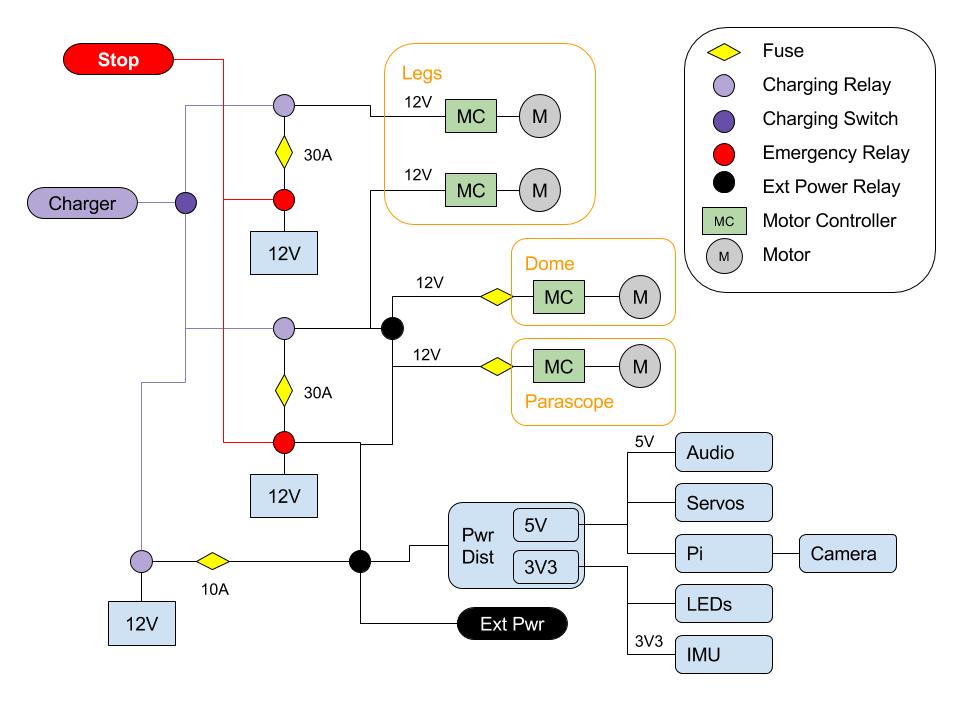
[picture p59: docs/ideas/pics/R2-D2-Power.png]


Use automotive relays to control power distribution. Basically hook them up
such that when 12V is attached for charging, they automatically disconnect the
batteries from the motors/robot and attach them to the charger.

Since all of the batteries are attached to the charging port, there is a charging
switch (manually operated) that a user must move to determine which battery will
be charged. This could be replaced with a circuit that measured the voltage of
each battery and determined which needed to be charged ... but let's start simple
first.

### Automotive Relay

The relays operate on 12V and can handle between 30A-40A depending on the type. They have 5 inputs:




- **Switch:** When 12V is applied across pins 85 and 86, a magnetic field is created and the relay switches from NC to NO path
- **Normally Closed (NC):** pins 30 and 87a are the default current path
- **Normally Open (NO):** pins 30 and 87 are the alternate current path

Some good references on relays:

- [How automotive relays work](https://www.youtube.com/watch?v=UAeKTlieYhw)
- [Explanation of different relay types](http://www.12voltplanet.co.uk/relay-guide.html)

### Batteries

The last version of R2 had multiple batteries, types, and voltages. This time
R2 will simplify to one type/voltage so we don't have to maintain different charger
and the added complexity that went along with that.

### Protection



Add a real emergency kill switch that cuts power to the motors. Prefer not to kill power to
the computer (typically not a good idea), plus, no one can get hurt by a raspberry pi.

The fuses are based on the last design. Not sure how much current is actually needed by the
leg motors nor what the continuous discharge rate of the selected batteries are.
All of the fuses will have to be properly sized.

### External Power

It is desired that R2 also serve as a static display. Being able to plug him into the
wall (automatically disable the leg motors so he can't move) and power the electronics
and maybe just the dome/periscope motors. In this configuration, the emergency safety
wouldn't work on the dome/periscope motors (remember the legs *are* disabled), but if
anything goes wrong, just pull the external power. Thinking a 12V 5A wall wart would work.

## Human Machine Interface





We could tie these to power up or reset the R2 electronics

## Motors

Re-selecting the Motor Controller, since it appears no engineering was done to select the
very expensive one we currently have.

Initial analysis is [here](motors.ipynb)

# How Ours Should Look







## Other Layouts



# Useful Links

- [www.artoo-detoo.net](http://www.artoo-detoo.net/tag/roboteq)

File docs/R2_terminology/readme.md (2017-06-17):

# R2-D2 Terminology and Parts

Here is an anatomy of an astromech, scrounged from the internet.

## Dome

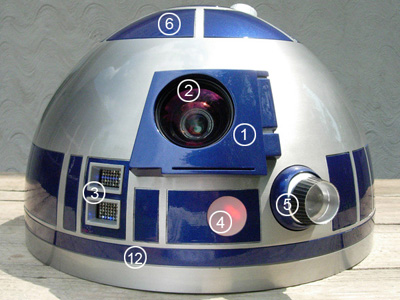
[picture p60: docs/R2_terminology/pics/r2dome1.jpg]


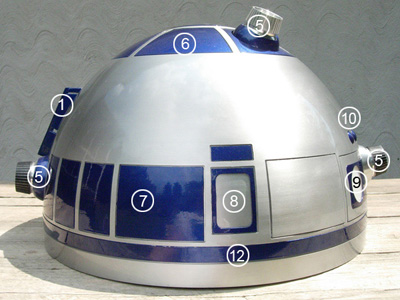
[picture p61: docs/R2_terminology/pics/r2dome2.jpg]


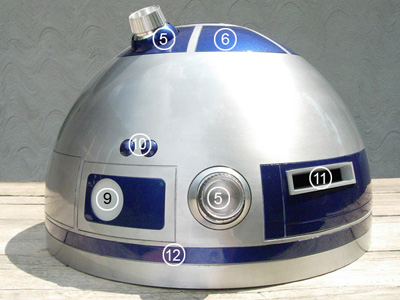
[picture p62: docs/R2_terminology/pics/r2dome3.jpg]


1. Radar Eye
2. Radar Eye Lens
3. Front Logic Display
4. Front PSI (Process State Indicator)
5. Holoprojectors (HPs)
6. Pie Panels
7. Dome Panels
8. P5 Picture Panel
9. Rear PSI (Process State Indicator)
10. Dome Bumps
11. Rear Logic Display
12. Dome Ring

## Body

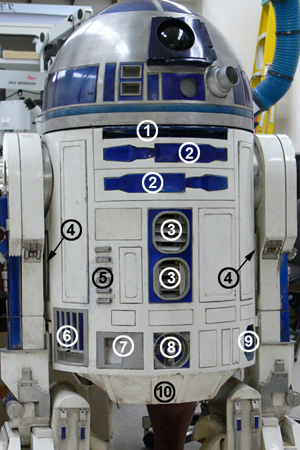
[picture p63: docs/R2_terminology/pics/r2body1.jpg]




1. Large Data Port (LDP)
2. Utility Arms
3. Front Vents
4. Side Vents
5. Coin Slots
6. Pocket Vents
7. Coin Returns
8. Power Couplings
9. Octagonal Ports
10. Skirt

## Legs

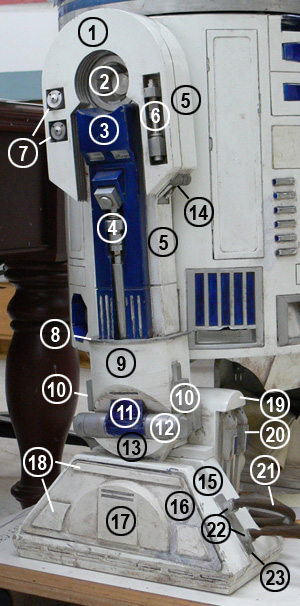
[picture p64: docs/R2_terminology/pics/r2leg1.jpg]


1. Shoulder Horseshoes
2. Shoulder Hub
3. Booster Covers
4. Leg Struts
5. Main Leg
6. Shoulder Hydraulics
7. Shoulder Buttons
8. Ankle Bracelet
9. Outer Ankle Sides
10. Ankle Details
11. Ankle Cylinder Wedges
12. Ankle Cylinders
13. Ankle Cylinder Holders
14. Under Shoulder Details
15. Main Foot shell
16. Foot Side Plate
17. Half Moon Details
18. Foot Details
19. Battery Boxes
20. Battery Box Harnesses
21. Foot Hoses
22. Knurled Fittings
23. Foot Strips

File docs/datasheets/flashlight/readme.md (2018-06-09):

# Holo Projectors (e.g., flashlights)





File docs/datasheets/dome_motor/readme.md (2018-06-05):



# 12V Motor with Encoder

- [Product link]()

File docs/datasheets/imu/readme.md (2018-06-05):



# Inertial Measurement Unit

The NXP Precision 9DoF board consists of two separate ICs, described in detail below:

FXOS8700 3-Axis Accelerometer/Magnetometer

- 2-3.6V Supply
- ±2 g/±4 g/±8 g adjustable acceleration range
- ±1200 µT magnetic sensor range
- Output data rates (ODR) from 1.563 Hz to 800 Hz
- 14-bit ADC resolution for acceleration measurements
- 16-bit ADC resolution for magnetic measurements

FXAS21002 3-Axis Gyroscope

- 2-3.6V Supply
- ±250/500/1000/2000°/s configurable range
- Output Data Rates (ODR) from 12.5 to 800 Hz
- 16-bit digital output resolution
- 192 bytes FIFO buffer (32 X/Y/Z samples)

- [Product link](https://www.adafruit.com/product/3463)

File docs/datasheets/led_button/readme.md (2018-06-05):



# LED Buttons

R2 uses both the on/off and momentary version. There are 2 sets of contact: NO and NC. There are also 4 pins: 5V, Red cathod, Green cathod, Blue cathod. If the cathod is HIGH, then the led is off. If the cathod is tied to ground, then the colored led turns on.

- [Datasheet](led_button.pdf)
- [Product link](https://www.adafruit.com/product/3423)

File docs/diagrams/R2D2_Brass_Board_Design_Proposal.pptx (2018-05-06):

## Brass Board Dimensions

## Wood Board Design


## Wood Board Dimensions


## Board Dome Dimensions


## Board Body Dimensions


## Board Leg Dimensions


## Brass Board Electronics Layout


## Dome Electronics Layout

Servos

Dome Motor


8x8 LED Color Matrices

Flashlight LEDs

Pushbuttons

Slip Ring

LED Driver

## Dome Electronics Dimensions


## Dome Electronics Dimensions (Left)


## Dome Electronics Dimensions (Right)


## Body Electronics Layout

PWM-Servo Controller


Raspberry Pi

Pololu Motor Controller

Orientation Sensor

Raspberry Pi
Camera

Amplifier

Arduino

Speaker

3.3 Voltage Regulator

Fan

Sabertooth Motor Controller

Current Sensor

5.0 Voltage Regulator

Battery

## Body Electronics Dimensions


## Body Electronics Dimensions (Top Half)


## Body Electronics Dimensions (Bottom Half)


## Leg Electronics Layout

RIGHT LEG


LEFT LEG


Keypad

Leg Motor & Gear Box

## Leg Electronics Dimensions (LEFT)


## Leg Electronics Dimensions (RIGHT)


All dimensions same as left leg.

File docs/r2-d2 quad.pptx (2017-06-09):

## Robotics: R2-D2

- Purpose: Build an R2-D2 Astromech Droid
- Scenario: Design, build, and deliver a robot capable of safe, independent operation. The team shall architect a complete hardware and software solution using a modern robotic principles. Update power, safety, and control systems for increased utility. Integrate sensors and develop software for human/robot interaction.
- Sponsor: DFEC
- Mentor: Maj Walchko

R2-D2 Key Sensors/Electronics:


Research Areas and Experiments
- Autonomous and Remotely Operated Systems
- Guidance, Navigation, and Controls
- Computer Vision
- Speech Recognition
- Linux Operating System
- Embedded Hardware and Software Systems
- Electronic and Power System Design
- Sensor Calibration and Fusion
- Testing and Integration


Raspberry Pi and Cameras


LIDAR


Arduino Mega


Ultrasonic

## Topics

- Navigation
  - Sensor fusion
  - IMU integration
  - INS development
- Vision
  - Color tracking
  - People id/tracking
  - Obstacle detection
  - Visual odometry
- Human/Machine
  - Command recognition
  - Remote operation

- Power system redesign
  - Simplify and reduce SWaP
  - Board design
- Hardware mods (?)
- Autonomy
  - Personality
- System engineering
  - Document HW/SW design and interfaces
  - Risk, trades, timeline
  - User manual
- Safety (PESHE)
  - For both building, maintaining, and ops

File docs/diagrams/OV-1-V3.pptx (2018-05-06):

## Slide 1

Camera

LEDs


Dome motors

R2D2 Capstone
OV-3
29-Nov-17 | V2.0

Servos

EMS Button

Speakers

Wifi Network

Leg Motors


PS4 Controller


Bluetooth


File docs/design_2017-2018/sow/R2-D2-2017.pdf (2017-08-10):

Design Project Description - AY 17-18 | Page 1

Department of Electrical Engineering USAF Academy
ECE 463/464, SE 491E/492E
Academic Year 2017-2018

### Design Project Description

R2D2¹
Version 1

Primary Project Mentor/Host Department: Maj Kevin Walchko, DFEC

Non DFEC Project Affiliate/Affiliated DF Department: N/A.

Customer/ Customer’s Agency: N/A.

Project Description: R2-D2 is a mascot for DFEC and its purpose is to demonstrate DFEC’s multi-disciplinary engineering projects, support DFEC and DF events and STEM outreach. The intent is, R2-D2 must be designed for and have proper documentation allowing easy maintenance for 10 yrs.

Detailed Description: The cadets shall design, build, test, document, and deliver an R2-D2 for their capstone. The capstone does not have to determine part lifetimes and deliver spares to support R2-D2’s operational lifetime of 10yrs. The key performance parameters (KPPs) described later are: safety, R2-D2’s appearance, R2-D2 like interaction with people, and simple operations.

Operational Scenario: R2-D2 shall be capable of the following operating modes:

1. Standby mode: When R2 software is started, it will enter this state and remain until commanded to exit. No motor (servos, legs, or dome) are allowed to run. This state produces and is capable of recording telemetry. This state is the only state where charging will occur. When the power plug is connected, the robot will change from whatever state it is in to this one.
2. Remote controlled mode: When commanded into this state, the robot will except commands from the joystick. The commands will be followed except where sensor detect hazards and prevent the operator from damaging the robot (e.g., the operator cannot drive R2-D2 down stairs). In this state, all motors are enabled.
3. Static display mode: When commanded into this state, the robot acts like a robotic static display. The leg motors are not enabled; however the dome motor is able to move. This mode is entered either by a software command or external power supplied to the robot which will trigger relays and automatically cut power to the leg motors.
4. Autonomous mode: When commanded into this mode, the robot will autonomous move and avoid obstacles using its onboard sensors. When any issue arises (i.e., motor currents exceeded, loss of sensors prohibiting safe operation, etc) the robot will immediately go to standby mode. Also in this mode, R2 should be able to detect boundaries marked on the ground and treat them like obstacles (most likely black electrical/duct tape).

1 Complete all entries occupied by text in italics.

Additional modes may need to be developed depending on design.

R2-D2’s Operations and Maintenance (O&M) shall be designed to be simple. R2-D2 shall charge off one charging cable that is easy to attach (see Episode IV, Luke Skywalker charging R2 on Tatoonie, or Episode V on Degobah). Turning R2-D2 on or off, changing operating modes, driving, or any other operating function shall follow Apples motto: “it just works.” Additionally, the assumption is parts may need to be replaced over the years, so everything needs to be accessible / modular for simple maintenance. Additionally, operation of R2-D2 is always safe, where onboard sensors ensure the user doesn’t damage the robot or hurt anyone else due to carelessness.

Deliverables: Cadets shall deliver a complete documentations package to support
O&M:
- A fully operational/functional R2D2
- A fully operational/functional brass board of R2-D2 suitable as a hallway display
- Complete R2D2 specification
- All design trades
- All parts sources and costs
- A complete power and weight budget
- Detailed build instructions with pictures
- Document all hardware, software, and electrical interfaces
- All mechanical designs developed this year
- All electrical/board designs developed this year
- A complete description of Linux setup so the operating system can be redone from the standard Linux image should the system become corrupted
- All source code in a git repository and fully commented
- An operator’s manual

Specifications: R2-D2 must meet the following specifications:

1. [KPP] R2 shall operate safely in all of the operating modes described above. Any loss of command or fault will automatically transition the robot into Standby mode.
2. [KPP] When the emergency stop (EMS) button is pressed, power shall be removed automatically to all motors (even under a fault condition that rendered the Linux computer inoperable), but all electronics shall continue to operate producing telemetry and status info.
a. The EMS shall be mounted approximately where R2's inhibitor switch is located in Episode IV.
3. R2's sensor suite shall allow:
a. Measure voltage and current at the leg motor batteries and electronics battery. When batteries are low, notify user and when a prescribed depth of discharge is reached, switch operating mode to standby until batteries are charged.

b. Sense orientation and switch to standby if R2 has fallen down (exceeds a pitch or roll in excess of a predefined value). R2 shall also emit warning sounds and flash displays periodically (time interval is TBD) to indicate its need for assistance.
c. Sense Earth's magnetic field, process the information into a heading (+/- 5 degrees), and use for navigation as needed
d. Sense angle of dome in order to point the dome in a defined direction, (+/-3 degrees)
e. Sense the environment in front of it visually and be capable of:
i. Detecting faces in imagery (50% of time, with faces occupying 10 % of the image)
ii. Detecting scene change (i.e., someone entering a room) in static display mode (50% likelihood of detection)
iii. [objective] Recognize specified individuals (full list is TBD, but for ex: Darth Vader, Luke, Han) under ideal conditions. Note, these do not have to be real people, just images of them.
iv. Streaming (mjpeg) to any standards compliant web browser
f. Measure distance travelled (odometry) to a resolution of 10cm across 5m.
g. R2 shall sense stairs and drop-offs (or absence of floor) 180 degrees (threshold) or 360 degrees (objective) around it along the floor plane for safety
h. R2 shall sense obstacles 180 degrees (threshold) or 360 degrees (objective) around it along the floor plane for safety
4. [KPP] While in static display mode, R2 shall sense the room and periodically interact with people passing by. The idea of "interacting" with people is TBD, but should in some way involve some or all of its capabilities: moving the dome, changing the displays, making sounds. The idea is to "entertain" visitors to the DFEC front office (or where ever R2 is put on display).
5. R2's interior shall be clean and designed to be presentation ready.
a. All cables will be routed and neat.
b. All electronics shall be neatly mounted
c. [objective] Interior lighting shall be setup to improve visitor inspection of engineering work
6. R2 shall have a modular design to support O&M
a. All cable shall have connectors for easy disconnecting
b. Design shall be modular and any interior component shall be removable for maintenance without having to cut, unglue, de-solder, or damage the robot in any way.
7. [KPP] R2 shall be returned to its proper appearance (as seen in Episode IV) with certain exceptions (e.g., emergency stop button) and some of the functions seen in the movies:
a. Holes in dome need to be filled in
b. Body needs to be re-assembled and outer structure (re)painted as necessary
c. Leg motors need to be hidden in the battery box
d. Front leg needs to be attached e. Skirt needs to be attached
f. Leg covers/decorations need to be attached
g. Leg and dome motors need to be properly mounted using the built in mounting holes
h. Dome rotates 360 deg
i. Dome doors open/close and TBD body panel doors via servos
j. [objective] Leg thrusters for R2-D2 to fly with as seen in Episode II
8. R2 shall produce and record telemetry for testing and O&M:
a. Power, current, voltage on batteries, motors, and power distribution (5V, 3.3V)
b. Camera images
c. Sensor data (TBD until identified for remote control and autonomous operations)
9. R2-D2’s will be filled with a lot of electronics that run hot, cadets shall make best effort to ensure proper cooling.
10. Human Machine Interface (HMI):
a. Telemetry: To aid in debugging/operations, HMI shall be defined for selected data and displayed/conveyed by R2 through a web server, display, sound, dome movement, or other method. The meanings shall be documented in the user manual of what these HMI mean.
b. [KPP] Operation: R2 shall be simple enough a 9 year old (or RPA pilot) can drive it (Remote Controlled Mode) or switch it into any other state. No command line ninja skills shall be required.
i. This may require more buttons, switches, or other HMIs to support this
c. In remote controlled mode, R2-D2 shall be driven via a wireless Bluetooth joystick connected directly to R2-D2
d. R2-D2 shall support connecting to a local Ethernet (this needs to be easily accessible to user) or wifi network.
e. R2-D2 shall provide its own wifi network, so users/visitor can connect directly to it and view telemetry or other interesting data (video stream), movie clips

Constraints
1. R2-D2 shall operate off a 12V power system (for distributing power and charging). Buck converters shall lower the voltage to support other voltage levels
2. R2-D2 shall be designed to operate in doors (smooth floors, handicapped ramps, temperature controlled) or outside under ideal conditions (not all-weather, roads/sidewalks, 70 degree F, no bad weather)
3. In Static Display Mode, R2-D2 shall be run off external 12V power (wall wart) plugged into a standard power outlet. The external power only runs the equipment in this mode and the leg motors are disconnected to prevent accidental activation

Equipment/Data/Software Furnished: DFEC has already developed a reference design and purchased a variety of parts to support that reference design. Additionally, key hardware was purchased for the project in 2010 that is furnished.

Software, either designed specifically for this project or useable by this project is listed here:

- https://pypi.python.org/pypi/ttastromech
- https://github.com/MomsFriendlyRobotCompany/mote
- https://pypi.python.org/pypi/nxp-imu
- https://pypi.python.org/pypi/mcp3208
- https://pypi.python.org/pypi/fake-rpi
- https://pypi.python.org/pypi/smc
- https://pypi.python.org/pypi/pysabertooth
- https://github.com/DFEC-R2D2/r2d2

Resources: Unfortunately, AY 16-17 R2-D2 program was a disaster, with no recoverable design, software, or hardware. The following resources are for guidance only:

- http://astromech.net (need to make an account)
- http://2geekswebdesign.com/astromech/
- http://www.artoo-detoo.net/

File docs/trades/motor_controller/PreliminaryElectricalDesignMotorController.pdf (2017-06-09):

Manufacturer | Feature Weight RoboteQ FeatuWeighRobo Claw Dimension FeatuWeighVortex | IFI Robotic Dimension FeatuWeighDimension FeatuWeighted FeaturFeatuWeighRoboteQ FeatuWeighRoboteQ FeatuWeighted Feature Score
Model | ax1500 | B0098 | Sabertooth 2x60 | 4QD‐VTX‐4Victor 884 Sabertooth 2x25 | SyRen 25 | Scorpion XXL V2 | SDC2130 | SDC1130
Go/No‐Go | Yes | No | Yes | No | No | Yes | Yes | Yes | Yes | Yes
Cost | 4 | 275 | 2 | 8 | 125 | 190 | 3 | 12 | 124 | 90 | 125 | 5 | 20 | 75 | 4 | 16 | 160 | 4 | 16 | 175 | 4 | 16 | 125 | 3 | 12
Operating Voltage | 12 ‐ 40 | 6 ‐ 30 | 6 ‐ 30 | 12 | 6 ‐ 15 | 6 ‐ 24 | 6 ‐ 24 | 6 ‐ 28 | 7 ‐ 30 | 10 ‐ 30
Number of Channels | | 2 | | | 2 | 2 | | | 1 | 1 | 2 | | | 1 | | | 2 | | | 2 | | | 1
Command Interface | 3 | | 4 | 12 | | | 5 | 15 | | | | 5 | 15 | | 5 | 15 | | 2 | 6 | | 5 | 15 | | 5 | 15
uC | ? | Yes | Yes | No | No | Yes | Yes | No | Yes | Yes
RS‐232, Simple | Yes | Yes | Yes | No | No | Yes | Yes | No | Yes | Yes Yes | Yes | Yes | No | No | Yes | Yes | No | Yes | Yes
RS‐232, Packet | No | Yes | Yes | No | No | Yes | Yes | No | Yes | Yes
RC | Yes | Yes | Yes | No | Yes | Yes | Yes | Yes | Yes | Yes
0 ‐ 5 V Analog | Yes | Yes | Yes | Yes | No | Yes | Yes | No | Yes | Yes
Control Modes | 3 | | 4 | 12 | | | 3 | 9 | | | | 3 | 9 | | 3 | 9 | | 3 | 9 | | 4 | 12 | | 4 | 12
Indep Ch | Yes | Yes | Yes | N/A | N/A | Yes | Yes | Yes | Yes | Yes
O‐L | Yes | Yes | Yes | Yes | Yes | Yes | Yes | Yes | Yes | Yes
C‐L Position | Yes | Yes | No | No | No | No | No | No | Yes | Yes
C‐L Speed | Yes | Yes | No | No | No | No | No | No | Yes | Yes
Current, Current, Max Cont. | 4 | 20 | 3 | 12 | 25 | 60 | 4 | 16 | 20 | 40 | 25 | 4 | 16 | 25 | 4 | 16 | 20 | 3 | 12 | 15 (5) | 2 | 8 | 20 | 3 | 12
Current, Max Trans. | 4 | 30 | 3 | 12 | 30 | 120 | 4 | 16 35 ? | ? | 50 | 4 | 16 | 45 | 4 | 16 | 45 | 3 | 12 | 20 (5) | 3 | 12 | 40 | 4 | 16
Current, Surge | 150 | ? | ? | ? | ? | ? | ? | ? | 50 (5) | 100
Current Limiter | 4 Yes | 5 | 20 | No | Yes (6) | 1 | 4 | No | No | Yes (6) | 1 | 4 Yes | 4 | 16 Yes | 3 | 12 Yes | 5 | 20 Yes | 5 | 20
Current Limiter Adjustment | 2 Yes | 3 | 6 No | No | 0 | 0 No | No | No | 0 | 0 No | 0 | 0 No | 0 | 0 Yes | 3 | 6 Yes | 3 | 6
Encoder Inputs | 3 2 Quad, 25 | 3 | 92 Quad, 15No | 3 | 9 No | No | No | 0 | 0 No | 0 | 0 No | 0 | 0 2 Quad, 30 | 3 | 91 Quad, 1 M 3 | 9
Emergency Stop Input | 4 Yes | 3 | 12 | No/Ext. Re Yes | 3 | 12 Yes | No/Ext. Re Yes | 3 | 12 Yes | 3 | 12 Yes | 3 | 12 Yes | 3 | 12 Yes | 3 | 12
Digital Inputs | 2 | 2 | 3 | 6 | 0 | 0 | 0 | 0 | 0 | 0 | 0 | 0 | 0 | 0 | 0 | 0 | 0 | 0 | 0 | 6 | 4 | 8 | 6 | 4 | 8
PWM Outputs | 4 16 kHz | 3 | 12 ? kHz | 24 kHz | 3 | 12 20 kHz | ? kHz | 32 kHz | 3 | 12 32 kHz | 3 | 12 ? kHz | 3 | 12 32 kHz | 3 | 12 32 kHz | 3 | 12
Four Quadrant Quadrant Operation Operation | Yes | Yes | Yes | Yes | Yes | Yes | Yes | Yes | Yes | Yes
BEC | 5 V, 100 mA | 5 V, 100 m5 V, 1 A | No | No | 5 V, 100 mA | 5 V, 100 mA | 5 V, ? mA | 5 V, 50 mA | 5 V, 100 mA
Housing/Mounting | No | No | No | No | Yes | No | No | No | No | No
Notes | (1) | (2) | (3) | (4) | (5) | (5)
Seller | http://www.robotmar http://wwwhttp://www.robotmar http://wwwhttp://wwwhttp://www.robotmarketplace.com/productshttp://www.robotmar http://www.robotmar http://www.roboteq.com/brushed‐dc‐motor‐controllers
Alt Seller | http://www.robotgear.com.au/Product.aspx/Details/479
Manufacturer | http://www.roboteq.com | http://www.dimensionengineering.com/Sab http://www.dimensionengineering.com/Sabertooth2X25.htm | http://www.roboteq.c http://www.roboteq.com
Product Score | | | | 121 | | | | 105 | | | | | 104 | | | 112 | | | 91 | | | 130 | | | 134

Notes
(1) Since max continuous and max transient current capabilities are well below the NPC‐2212 stall current, and no active current limiting, motor controller may be unsuitable.
Presumably, if the motor controller output current is above the max continuous limit for an extended period of time, then the motor controller may enter thermal shutdown, rather than current limiting.
(2) Could handle NPC‐2212 operating envelope without current limiting.
For closed‐loop speed control (or closed‐loop position control), would require uC to process encoder feedback signals and implement closed‐loop control laws.
(3) Poor documentation.
(4) No manual?
(5) 20 A for up to 30 s, which far exceeds the time required to execute the worst case/abrupt stopping maneuver.
(6) Sabertooth 2x25 and 2x60 will shut the outputs off if they are thermally above a threshold or if it senses current above the rated maximum. The outputs will stay off until the error condition has lifted. SyRens are a bit more intelligent in this manner. They measure cycle by cycle and will reduce PWM and output current to compensate if measured current is above the threshold.

s/sdc1130‐40a‐brushed‐dc‐motor‐controller

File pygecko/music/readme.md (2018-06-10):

# Techno Music

I downloaded these from [Reverbnation](https://www.reverbnation.com/Shad3yD3stiny)

## Artist Bio



### Shad3dy D3stiny

Originally from the U.K and now I reside in Australia, I did not produce any of these tracks I just remixed them, tweaked them and added samples and manipulated them, they were made for fun and entertainment, for sharing with anyone who cared to take a listen. I am not a professional DJ and I do not make money off of this. I do not have any rights from LucasFilms , WarnerBros or any Music artists such as Moby and bentframe. If someone wants to get mad about it, sheese I'm sorry, gimmie a break. Gimmie a break, gimmie a break. Break me off a piece of that. What was it again? I just love experimenting with music I have mixed not just techno and hiphop, but also pink Floyd and music from movies I love! I adore mixing starwars, matrix, Snatch and other movies quotes and effects into techno, trance, Drum-n-Bass and hip hop.

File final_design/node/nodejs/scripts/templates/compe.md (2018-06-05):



# Computer Engineers

Computer systems are an integral part of every aspect of Air Force operations. These systems range from embedded devices that perform a specific function in a weapon system to massively-parallel supercomputers used to simulate an air campaign.

Because today’s computing systems are so sophisticated, computer engineering has evolved. Computer engineers take a true “systems” view toward computing design, combining the algorithm-design skills of a computer scientist with the hardware-design talents of an electrical engineer. Computer engineering majors acquire these skills through an interdisciplinary approach that intermingles courses from computer science with offerings from electrical and computer engineering. This program provides the broad, varied background an engineer needs to succeed in this dynamic field.

The Computer Engineering major is accredited by the Engineering Accreditation Commission of ABET, www.abet.org.

## Potential Jobs Within the Air Force

- 62E – Developmental Engineer
- 17D – Cyber Operator

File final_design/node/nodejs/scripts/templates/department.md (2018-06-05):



# Department of Electrical and Computer Engineering

The 21st century is an increasingly electrical one, both on the battlefield and in the workplace. Without electrical engineers, modern computers, control systems or even high-fidelity sound systems would not be possible. Computer engineers combine the hardware-design talents of an electrical engineer with the algorithm-design skills of a computer scientist to take a true “systems” view toward computing design.

## The Department of Electrical & Computer Engineering offers five areas of study:

1. Electronics – focuses on electronic design, components and applications; ideal for cadets interested in graduate studies in electrical engineering, physics, medicine or other technical fields
1. Communications – helps cadets understand satellite communications and systems, telephones, stealth technology and advanced radar systems
1. Computer Systems – explores fundamentals and advanced concepts of modern computer systems and digital hardware design
1. Controls – emphasizes the analysis and design of automatic control systems; includes courses taught by the Department of Astronautics
1. Universal Area – allows cadets to take any two electrical engineering options

Regardless of the field you chose, one thing is clear, your knowledge and skills will be in high demand both in the Air Force and in public and private industries. Set your career off on the best foot with the United States Air Force Academy’s Department of Electrical & Computer Engineering—ranked #5 by U.S. News’ Best Colleges List.

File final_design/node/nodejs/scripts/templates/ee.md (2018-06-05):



# Electrical Engineers

The battlefield of the 21st century is increasingly an electronic one, and electrical engineers (EEs) lead the way in creating the technology that dominates there. Without EEs, modern computers, control systems or even high-fidelity sound systems would not be possible.

From sophisticated sensors that detect and locate targets to the terrain following radar that aircrews depend on to “smart” computer guided munitions that attack targets with amazing accuracy, the modern military would not have its current capabilities without electronics and EEs.

The electrical engineering major covers the basic principles behind these systems and provides graduates with valuable insight into their operation. Officers who understand the technology and can use it to their advantage will have the “combat edge” over the opponent.

The Electrical Engineering major is accredited by the Engineering Accreditation Commission of ABET, www.abet.org.

## Potential Jobs Within the Air Force

- 62E – Developmental Engineer
- 17D – Cyber Operator
- 32E – Civil Engineer

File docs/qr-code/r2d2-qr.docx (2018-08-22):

Learn more about the ECE Department

1. Join R2-D2’s wifi network: r2d2
2. Password: robotsarecool
3. Scan the QR code below
  a. Or point your browser to 10.10.10.1:9000


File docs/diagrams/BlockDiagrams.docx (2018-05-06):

Operational View


System Block Diagram


Software Block Diagram


R2D2 Block Diagrams

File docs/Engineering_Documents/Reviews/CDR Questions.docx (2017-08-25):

CDR Questions from

Defense Acquisition Guidebook

Typical CDR success criteria include affirmative answers to the following exit questions:

1. Does the status of the technical effort and design indicate operational test and evaluation success (operationally effective and suitable)?
2. Does the detailed design (hardware and software) including interface descriptions completed, as disclosed, satisfy the SOW?
3. Has the system product baseline been established and documented to enable hardware fabrication and software coding to proceed with proper configuration management?
4. Has the detailed design satisfied sustainment and Human Systems Integration requirements?
5. Are adequate processes and metrics in place for the program to succeed?
6. Are the risks known and manageable for testing in support of developmental and operational evaluation objectives?
7. Is the program schedule executable (technical risks)?
8. Is the program executable with the approved product baseline?
9. Are all Critical Safety Items and Critical Application Items identified?
10. Is the software functionality in the approved product baseline consistent with the updated software metrics and resource-loaded schedule?
11. Have key product characteristics having the most impact on system performance, assembly, cost, reliability, and sustainment or safety been identified?
12. Have the critical manufacturing processes that affect the key characteristics been identified and their capability to meet design tolerances determined?
13. Have manufacturing processes been demonstrated in a production representative environment?
14. Are detailed trade studies and system producibibility assessments underway?
15. Are long lead procurement plans in place and has the supply chain been assessed?

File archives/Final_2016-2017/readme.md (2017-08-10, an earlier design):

# 2017 R2D2 Capstone

"what a piece of junk" - Luke Skywalker upon seeing the *Falcon*



















## Issues

- Impassable quagmire of wires/cables which led to things getting shorted out
- Tape and hot glue literally held the thing together, but the next day, things start to
fall off ... so much for duct tape being the greatest. Also, there is a huge mess of gorilla glue and epoxy everywhere making it look and feel (the whole thing is sticky) terrible
- Raspberry Pi camera is shorted out after being wedged (mounted) between some aluminum
- None of the LEDs are mounted, instead the holes are filled with tin foil (maybe it blocks the dark side's attempts at controlling R2?)
- Wood screws are used instead of bolts and they are falling out
- Breadboards, jumper wires and terrible soldering create a potential fire hazard
- Emergency kill switch is not correct and would not be effective in an emergency situation
- All of the motors are improperly mounted ... generally they are strapped on to the body instead of using the mounting holes built into them
- The battery boxes don't cover the leg motors
- The batteries are press fit into the battery boxes and cannot be removed
- The battery trade was done incorrectly and our batteries do not supply the correct current needed. Because the battery is stressed, it will have a much shorter life span than expected
- The motor driver is grossly oversized, bulky, and insanely expensive
- There is no plan for how to mount anything inside and nothing is modular
    - There are no connectors anywhere, everything is soldered together or multiple wire nuts were used to connect multiple lengths of short wires together into a larger wire
    - In order to remove the motor drive, the wires to it had to be cut ... however, a couple were just twisted together and wrapped in tap (no soldering)
- The software is written wrong (amateur at best) and incapable of being useful
- The front wheel was never mounted, instead, some silly wheel was on it. This made R2 lean forward and very susceptible to tipping over ... which happened
- No architectural diagrams or documentation on interfaces or software ... no clue what did what.

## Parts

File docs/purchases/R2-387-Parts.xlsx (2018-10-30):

ECE-387
No. | Name | Source | ID | Qnty | cost | Total
1 | Miniature WiFi (802.11b/g/n) Module | Adafruit | 814 | 10 | 11.95 | 119.5
2 | [Upgraded Capacity] Anker Astro E1 6700mAh Ultra-Compact Portable External Battery Charger with PowerIQ Technology (Black) | Amazon | B06XS9RMWS | 10 | 18.99 | 189.9
3
4
5
6
7
8
9
10
sum |  |  |  |  |  | 309.4
R2-D2
No. | Name |  | ID | Qnty | cost | Total
1 | 50:1 Metal Gearmotor 37Dx70L mm with 64 CPR Encoder 200 rpm 12V | Pololu.com | 2824 | 2 | 39.95 | 79.9
2 | 6 Pack - OLS 12V DC 40/30 Amp 5-Pin SPDT Automotive Relay Harness Set | amazon.com | B01KVZ2MU4 | 2 | 10.99 | 21.98
3 | Sharp GP2Y0A51SK0F Analog Distance Sensor 2-15cm | Pololu.com | 2450 | 15 | 7.95 | 119.25
4 | Pololu Simple Motor Controller 18v7 | Pololu.com | 1373 | 1 | 31.95 | 31.95
5 | Adafruit Pro Trinket - 5V 16MHz | adafruit.com | 2000 | 2 | 9.95 | 19.9
6 | Adafruit Pro Trinket - 3V 12MHz | adafruit.com | 2010 | 2 | 9.95 | 19.9
7 | us digital e4t encoder, 360 cpr, 1/4", single ended | usdigital.com | E4T-360-250-S-H-D-B | 4 | 24.81 | 99.24
8 | Raspberry Pi 3 - Model B - ARMv8 with 1G RAM | adafruit.com | 3055 | 4 | 39.95 | 159.8
9
10
sum |  |  |  |  |  | 551.92

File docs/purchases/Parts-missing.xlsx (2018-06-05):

Electronics for R2D2 brass plate and body
No. | Source | Part Number | Item | Description | Price | Quantity | Sum | Link
1 | sparkfun.com | 13104 | LED Flashlight | LED - 3W Aluminum PCB (5 Pack, Warm White) | $7.95 | 2 | $15.90 | https://www.sparkfun.com/products/13104
2 | sparkfun.com | 13716 | LED Driver | FemtoBuck LED Driver | $7.95 | 3 | $23.85 | https://www.sparkfun.com/products/13716
3 | sparkfun.com | 14577 | TFMini - Mocro LiDAR | Lidar | $39.95 | 2 | $79.90 | https://www.sparkfun.com/products/14577
4 | sparkfun.com | 10288 | DC Barrel Jack - female | DC Barrel Jack Adapter - Female | $2.95 | 3 | $8.85 | https://www.sparkfun.com/products/10288
5 | sparkfun.com | 10287 | DC Barrel Jack - Male | DC Barrel Jack Adapter - Male | $2.95 | 3 | $8.85 | https://www.sparkfun.com/products/10287
6 | sparkfun.com | 9873 | FTDI Basic Breakout 3.3V | usb-to-serial converter | $14.95 | 2 | $29.90 | https://www.sparkfun.com/products/9873
7 | sparkfun.com | 14277 | Raspberry Pi Zero W | Raspberry Pi Zero W | $10.00 | 2 | $20.00 | https://www.sparkfun.com/products/10287
 | Sum |  |  |  |  |  | $187.25

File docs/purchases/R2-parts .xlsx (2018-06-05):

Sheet: Parts-Needed
R2-D2 Parts
No. | Source | Part Number | Item | Price | Quantity | Sum | Link
1 | Mouser | 22-03-5035 | Molex Connector | $0.42 | 20 | $8.34 | https://www.mouser.com/ProductDetail/Molex/22-03-5035
2 | Mouser | LRS-350-12 | Mean Well Switching Power Supply 12V | $33.90 | 1 | $33.90 | https://www.mouser.com/ProductDetail/MEAN-WELL/LRS-350-12
3 | Sparkfun | 14643 | Raspberry Pi 3 B+ (the new one) | $39.95 | 2 | $79.90 | https://www.sparkfun.com/products/14643
4 | Sparkfun | 14577 | Tfmini lidar | $40.00 | 2 | $80.00 | https://www.sparkfun.com/products/14577
5 | Sparkfun | 13906 | 8 ch mux | $1.95 | 2 | $3.90 | https://www.sparkfun.com/products/13906
6 | amazon | b005vqbxv8 | Pink Racquetball balls | $6.00 | 2 | $12.00 | https://www.amazon.com/Wilson-Racquetball-Ball-Can-Pink/dp/B005VQBXV8?s=sporting-goods
7 | amazon | b003mxmjx8 | Tenergy 6-12v NiMH charger | $17.00 | 1 | $17.00 | https://www.amazon.com/Tenergy-Universal-Battery-Charger-Batteries/dp/B003MXMJX8?s=sporting-goods
 | Sum |  |  |  |  | $235.04

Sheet: Sheet1
 |  | ns
1000000 | 1e-06 | 1000
110000000000 | 9.090909091e-12 | 110
 | 2298850.575 | 435

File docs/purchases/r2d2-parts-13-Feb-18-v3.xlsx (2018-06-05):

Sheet: Parts-Needed
R2-D2 Parts
No. | Source | Part Number | Item | Description | Price | Quantity | Sum | Link
SW/Sensors
1 | adafruit.com | 169 | Servo | servo | $15.00 | 3 | $45.00 | https://www.adafruit.com/product/169
2 | adafruit.com | 1196 | Slip ring | Slip Ring with Flange - 22mm diameter, 12 wires, max 240V @ 2A | $19.95 | 2 | $39.90 | https://www.adafruit.com/product/1196
3 | sparkfun.com | 13104 | LED Flashlight | LED - 3W Aluminum PCB (5 Pack, Warm White) | $7.95 | 1 | $7.95 | https://www.sparkfun.com/products/13104
4 | sparkfun.com | 13716 | LED Driver | FemtoBuck LED Driver | $7.95 | 2 | $15.90 | https://www.sparkfun.com/products/13716
5 | pololu.com | 1372 | Dome Motor Controller | Pololu Simple Motor Controller 18v7 (Fully Assembled) | $33.95 | 1 | $33.95 | https://www.pololu.com/product/1372
6 | adafruit.com | 815 | PWM-Servo Controller | PWM/Servo Driver - I2C interface - PCA9685 | $14.95 | 2 | $29.90 | https://www.adafruit.com/product/815
7 | pololu.com | 2857 | 3.3V Converter | Pololu 3.3V, 2.6A Step-Down Voltage Regulator D24V22F3 | $8.95 | 2 | $17.90 | https://www.pololu.com/product/2857
8 | pololu.com | 2866 | 5V Converter | Pololu 5V, 9A Step-Down Voltage Regulator D24V90F5 | $27.95 | 2 | $55.90 | https://www.pololu.com/product/2866
9 | adafruit.com | 3055 | Raspberry Pi | Raspberry pi v3 | $35.00 | 2 | $70.00 | https://www.adafruit.com/product/3055
10 | amazon.com | B01MFG0O6Z | Lithium Phosphate Battery | 12V 35Ah Motorcycle Battery (Lithium Iron Phosphate) | $209.99 | 1 | $209.99 | https://www.amazon.com/Lithium-Phosphate-480CCA-Battery-Automotive/dp/B01MFG0O6Z
11 | mouser.com | 538-53253-0370 | Molex micro latch | Molex microlatch 3 position | $0.14 | 30 | $4.14 | https://www.mouser.com/ProductDetail/Molex/53253-0370
12 | mouser.com | 538-22-03-5035 | Molex connector | Molex header 3 position | $0.42 | 20 | $8.34 | https://www.mouser.com/ProductDetail/538-22-03-5035
13 | mouser.com | 621-AZ1117IH-5.0TRG1 | smd 5v regulator | 5v regulator, SOT-223-3 | $0.27 | 20 | $5.44 | https://www.mouser.com/ProductDetail/621-AZ1117IH-5.0TRG1
14 | mouser.com | LTST-C150TBKT | smd led | 1206 blue led | $0.29 | 20 | $5.80 | https://www.mouser.com/ProductDetail/859-LTST-C150TBKT
15 | mouser.com | LTST-C150EKT | smd led | 1206 red led | $0.18 | 20 | $3.60 | https://www.mouser.com/ProductDetail/859-LTST-C150EKT
16 | mouser.com | LTST-C150KFKT | smd led | 1206 orange led | $0.17 | 20 | $3.40 | https://www.mouser.com/ProductDetail/859-LTST-C150KFKT
17 | mouser.com | LTST-C150GKT | smd led | 1206 green led | $0.17 | 20 | $3.40 | https://www.mouser.com/ProductDetail/859-LTST-C150GKT
18 | sparkfun.com | 10288 | DC Barrel Adaptor | DC Barrel Jack Adapter - Female | $2.95 | 3 | $8.85 | https://www.sparkfun.com/products/10288
19
 | Sum |  |  |  |  |  | $569.36

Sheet: FundingBudget
 |  | % diff | T/g
54.6 | 16.7 | 2.269461078 | 0.02747252747
1.5 | 0.39 | 2.846153846 | 0.02335329341

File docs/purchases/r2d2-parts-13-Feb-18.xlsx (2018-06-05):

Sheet: Parts-Needed
R2-D2 Parts
No. | Source | Part Number | Item | Description | Price | Quantity | Sum | Link
SW/Sensors
1 | adafruit.com | 169 | Servo | servo | $15.00 | 3 | $45.00 | https://www.adafruit.com/product/169
2 | adafruit.com | 1196 | Slip ring | Slip Ring with Flange - 22mm diameter, 12 wires, max 240V @ 2A | $19.95 | 2 | $39.90 | https://www.adafruit.com/product/1196
3 | sparkfun.com | 13104 | LED Flashlight | LED - 3W Aluminum PCB (5 Pack, Warm White) | $7.95 | 1 | $7.95 | https://www.sparkfun.com/products/13104
4 | sparkfun.com | 13716 | LED Driver | FemtoBuck LED Driver | $7.95 | 2 | $15.90 | https://www.sparkfun.com/products/13716
5 | pololu.com | 1372 | Dome Motor Controller | Pololu Simple Motor Controller 18v7 (Fully Assembled) | $33.95 | 1 | $33.95 | https://www.pololu.com/product/1372
6 | adafruit.com | 815 | PWM-Servo Controller | PWM/Servo Driver - I2C interface - PCA9685 | $14.95 | 2 | $29.90 | https://www.adafruit.com/product/815
7 | pololu.com | 2857 | 3.3V Converter | Pololu 3.3V, 2.6A Step-Down Voltage Regulator D24V22F3 | $8.95 | 2 | $17.90 | https://www.pololu.com/product/2857
8 | pololu.com | 2866 | 5V Converter | Pololu 5V, 9A Step-Down Voltage Regulator D24V90F5 | $27.95 | 2 | $55.90 | https://www.pololu.com/product/2866
9 | adafruit.com | 3055 | Raspberry Pi | Raspberry pi v3 | $35.00 | 2 | $70.00 | https://www.adafruit.com/product/3055
10 | sparkfun.com | 14557 | Tfmini - LiDAR | TFMini - Micro LiDAR Module | $39.95 | 6 | $239.70 | https://www.sparkfun.com/products/14577
11 | amazon.com | B01MFG0O6Z | Lithium Phosphate Battery | 12V 35Ah Motorcycle Battery (Lithium Iron Phosphate) | $209.99 | 1 | $209.99 | https://www.amazon.com/Lithium-Phosphate-480CCA-Battery-Automotive/dp/B01MFG0O6Z
12
13
14
15
16
 | Sum |  |  |  |  |  | $766.09

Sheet: FundingBudget
No. | Part | Unit Price | Quantity | Sum
1 | Ultrasonic Sensor (5 pieces) | $9.99 | 2 | $19.98
2 | IR Sensor | $6.99 | 8 | $55.92
3 | Orientation Sensor | $14.95 | 3 | $44.85
4 | Raspberry Pi Camera | $19.95 | 2 | $39.90
5 | Servo | $5.95 | 14 | $83.30
6 | Speaker | $1.95 | 3 | $5.85
7 | 8x8 LED Matrix with Backpack | $15.95 | 16 | $255.20
8 | LED Flashlight (5 pieces) | $7.95 | 2 | $15.90 | Electronics Total
9 | LED Driver | $7.95 | 3 | $23.85 | $1055.89
10 | Simple Motor Controller | $33.95 | 2 | $67.90
11 | Sabertooth Motor Controller | $124.99 | 2 | $249.98
12 | PWM-servo Controller | $14.95 | 2 | $29.90
13 | Voltage Regulator (12V to 3.3V) | $8.95 | 3 | $26.85
14 | Voltage Regulator (12V to 5.0V) | $27.95 | 3 | $83.85
15 | LED Fan | $14.99 | 1 | $14.99
16 | WiFi Adapter | $8.95 | 1 | $8.95
17 | MicroSD Card | $10.41 | 2 | $20.82
18 | 3x4 Keypad | $3.95 | 2 | $7.90
19 | Dome | $490.00 | 1 | $490.00
20 | Outer Feet | $350.00 | 1 | $350.00
21 | Center Feet | $150.00 | 1 | $150.00 | Electrical & Mechanical Total
22 | Silver ABS Filament | $50.00 | 1 | $50.00 | $1319.00
23 | Motorcycle Battery | $210.00 | 1 | $210.00
24 | Smart Charging Cable | $57.00 | 1 | $57.00
25 | Entension Cord | $12.00 | 1 | $12.00
Total System Cost |  |  |  | $2374.89
Total Alloted for Project |  |  |  | $3000.00
Slack Budget |  |  |  | $625.11

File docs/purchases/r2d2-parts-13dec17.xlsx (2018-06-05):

R2-D2 Parts
No. | Source | Part Number | Item | Description | Price | Quantity | Sum | Link
SW/Sensors
1 | amazon.com | 41111926 | Ultrasonic Sensor | 5PCS of HC-SR04 Ultrasonic Module Distance Sensor | $9.99 | 2 | $19.98 | https://www.amazon.com/Gowoops-Ultrasonic-Distance-Measuring-Transducer/dp/B00UJA1TAQ?s=industrial
2 | amazon.com | AREEY507 | IR Sensor | Infrared Obstacle Avoidance Sensor KY-032 4pin | $6.99 | 8 | $55.92 | https://www.amazon.com/AuBreey-Infrared-Obstacle-Avoidance-Arduino/dp/B072NZC8VT?s=industrial
3 | adafruit.com | 3463 | Orientation Sensor | Adafruit Precision NXP 9-DOF Breakout Board - FXOS8700 + FXAS21002 | $14.95 | 3 | $44.85 | https://www.adafruit.com/product/3463
4 | adafruit.com | 3099 | Pi Camera | Raspberry Pi Camera Board V2.1 | $29.95 | 3 | $89.85 | https://www.adafruit.com/product/3099
5 | robotshop.com | RB-Hit-87 | Standard Servo | servo | $15.64 | 12 | $187.68 | http://www.robotshop.com/en/hitec-hs-485hb-servo-motor.html
6 | adafruit.com | 1314 | Speaker | Speaker - 3" Diameter - 4 Ohm 3 Watt | $1.95 | 3 | $5.85 | https://www.adafruit.com/product/1314
7 | adafruit.com | 902 | LED Matrix w/ Backpack | Adafruit Bicolor LED Square Pixel Matrix with I2C Backpack | $15.95 | 18 | $287.10 | https://www.adafruit.com/product/902
8 | pololu.com | 1372 | Dome Motor Controller | Pololu Simple Motor Controller 18v7 (Fully Assembled) | $33.95 | 1 | $33.95 | https://www.pololu.com/product/1372
9 | robotshop.com | RB-Dim-47 | Leg Motor Controller | Sabertooth Dual 2x32A Motor Driver | $124.99 | 1 | $124.99 | http://www.robotshop.com/en/sabertooth-dual-2x32a-6v-24v-regenerative-motor-driver.html
10 | adafruit.com | 815 | PWM-Servo Controller | PWM/Servo Driver - I2C interface - PCA9685 | $14.95 | 2 | $29.90 | https://www.adafruit.com/product/815
11 | pololu.com | 2851 | Voltage Converter - 1 | Pololu 5V, 5A Step-Down Voltage Regulator D24V50F5 | $14.95 | 3 | $44.85 | https://www.pololu.com/product/2851
12 | pololu.com | 2866 | Voltage Converter - 2 | Pololu 5V, 9A Step-Down Voltage Regulator D24V90F5 | $27.95 | 3 | $83.85 | https://www.pololu.com/product/2866
13 | pololu.com | 2857 | Voltage Converter - 3 | Pololu 3.3V, 2.6A Step-Down Voltage Regulator D24V22F3 | $8.95 | 3 | $26.85 | https://www.pololu.com/product/2857
14 | amazon.com | 9050017 | LED Fan | Corsair Air Series 1200 RPM High Airflow - Blue LED | $14.99 | 1 | $14.99 | https://www.amazon.com/gp/product/B00F6S0XZI
15 | amazon.com | SDSQUAR-016G-GN6MA | SD Card | Sandisk Ultra 16GB Micro SD with Adapter | $10.41 | 3 | $31.23 | https://www.amazon.com/Sandisk-Ultra-Micro-UHS-I-Adapter/dp/B073K14CVB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
16 | adafruit.com | 419 | Keypad | Membrane 3x4 Matrix Keypad + extras | $3.95 | 2 | $7.90 | https://www.adafruit.com/product/419
17 | usdigital.com | E4T-360-250-S-H-D-B | US Digital encoders for legs | us digital e4t encoder, 360 cpr, 1/4", single ended | $24.81 | 2 | $49.62 | usdigital.com
18 | adafruit.com | 3055 | Raspberry Pi | Raspberry pi v3 | $35.00 | 2 | $70.00 | https://www.adafruit.com/product/3055
19 | amazon.com?? |  | Acitone | 3d printing | $12.00 | 1 | $12.00 | I am told you know
20 | amazon.com?? |  | Metalic ABS | 3d printing | $50.00 | 1 | $22.99 | http://www.esun3d.net/products/104.html
21 | adafruit | 3006 | 3W Amp | Adafruit I2S 3W Class D Amplifier Breakout - MAX98357A | $5.95 | 3 | $17.85 | https://www.adafruit.com/product/3006
22
23
24
 | Sum |  |  |  |  |  | $1262.20
 | 1.458333333

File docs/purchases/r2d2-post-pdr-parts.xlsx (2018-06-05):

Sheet: Parts-Needed
R2-D2 Parts
No. | Source | Part Number | Item | Description | Price | Quantity | Sum | Link
SW/Sensors
1 | amazon.com | 41111926 | Ultrasonic Sensor | 5PCS of HC-SR04 Ultrasonic Module Distance Sensor | $9.99 | 2 | $19.98 | https://www.amazon.com/Gowoops-Ultrasonic-Distance-Measuring-Transducer/dp/B00UJA1TAQ?s=industrial
2 | amazon.com | AREEY507 | IR Sensor | Infrared Obstacle Avoidance Sensor KY-032 4pin | $6.99 | 8 | $55.92 | https://www.amazon.com/AuBreey-Infrared-Obstacle-Avoidance-Arduino/dp/B072NZC8VT?s=industrial
3 | adafruit.com | 3463 | Orientation Sensor | Adafruit Precision NXP 9-DOF Breakout Board - FXOS8700 + FXAS21002 | $14.95 | 3 | $44.85 | https://www.adafruit.com/product/3463
4 | adafruit.com | 3099 | Pi Camera | Raspberry Pi Camera Board V2.1 | $29.95 | 2 | $59.90 | https://www.adafruit.com/product/3099
5 | adafruit.com | 169 | Servo | servo | $15.00 | 14 | $210.00 | https://www.adafruit.com/product/169
6 | adafruit.com | 1314 | Speaker | Speaker - 3" Diameter - 4 Ohm 3 Watt | $1.95 | 3 | $5.85 | https://www.adafruit.com/product/1314
7 | adafruit.com | 902 | LED Matrix w/ Backpack | Adafruit Bicolor LED Square Pixel Matrix with I2C Backpack | $15.95 | 16 | $255.20 | https://www.adafruit.com/product/902
8 | sparkfun.com | 13104 | LED Flashlight | LED - 3W Aluminum PCB (5 Pack, Warm White) | $7.95 | 2 | $15.90 | https://www.sparkfun.com/products/13104
9 | sparkfun.com | 13716 | LED Driver | FemtoBuck LED Driver | $7.95 | 3 | $23.85 | https://www.sparkfun.com/products/13716
10 | pololu.com | 1372 | Dome Motor Controller | Pololu Simple Motor Controller 18v7 (Fully Assembled) | $33.95 | 2 | $67.90 | https://www.pololu.com/product/1372
11 | robotshop.com | RB-Dim-47 | Leg Motor Controller | Sabertooth Dual 2x32A Motor Driver | $124.99 | 1 | $124.99 | http://www.robotshop.com/en/sabertooth-dual-2x32a-6v-24v-regenerative-motor-driver.html
12 | adafruit.com | 815 | PWM-Servo Controller | PWM/Servo Driver - I2C interface - PCA9685 | $14.95 | 2 | $29.90 | https://www.adafruit.com/product/815
13 | pololu.com | 2858 | Voltage Converter - 1 | Pololu 5V, 2.5A Step-Down Voltage Regulator D24V22F5 | $8.95 | 3 | $26.85 | https://www.pololu.com/product/2858
14 | pololu.com | 2866 | Voltage Converter - 2 | Pololu 5V, 9A Step-Down Voltage Regulator D24V90F5 | $27.95 | 3 | $83.85 | https://www.pololu.com/product/2866
15 | amazon.com | 9050017 | LED Fan | Corsair Air Series 1200 RPM High Airflow - Blue LED | $14.99 | 1 | $14.99 | https://www.amazon.com/gp/product/B00F6S0XZI
16 | canakit.com |  | Wifi Adapter | Raspberry Pi WiFi Adapter | $8.95 | 1 | $8.95 | https://www.canakit.com/raspberry-pi-wifi.html
17 | amazon.com | SDSQUAR-016G-GN6MA | SD Card | Sandisk Ultra 16GB Micro SD with Adapter | $10.41 | 2 | $20.82 | https://www.amazon.com/Sandisk-Ultra-Micro-UHS-I-Adapter/dp/B073K14CVB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
18 | adafruit.com | 419 | Keypad | Membrane 3x4 Matrix Keypad + extras | $3.95 | 2 | $7.90 | https://www.adafruit.com/product/419
19 | usdigital.com | E4T-360-250-S-H-D-B | US Digital encoders for legs | us digital e4t encoder, 360 cpr, 1/4", single ended | $24.81 | 2 | $49.62 | usdigital.com
20 | adafruit.com | 3055 | Raspberry Pi | Raspberry pi v3 | $35.00 | 4 | $140.00 | https://www.adafruit.com/product/3055
21
22
23
24
Electrical
1 | amazon.com | B01MFG0O6Z | Lithium Phosphate Battery | 12V 35Ah Motorcycle Battery (Lithium Iron Phosphate) | $209.99 | 2 | $419.98 | https://www.amazon.com/Lithium-Phosphate-480CCA-Battery-Automotive/dp/B01MFG0O6Z
2 | amazon.com | G3500 | Smart Battery Charger | Charger that measures+displays health and charge level of battery | $59.95 | 1 | $59.95 | https://www.amazon.com/gp/product/B004LWVEKS/ref=ask_ql_qh_dp_hza
3 | amazon.com | GC004 | Charger Extension Cable | Extension cable to charge outside of robot (charger mounted internally) | $11.95 | 1 | $11.95 | https://www.amazon.com/NOCO-Genius-GC004-Extension-Cable/dp/B004LWV0GQ
4 | TBD | TBD | Relays | TBD | $12.00 | 2 | $24.00
5 | TBD | TBD | connectors | various connectors | $50.00 | 1 | $50.00
6 | TBD | TBD | wire/cables | various
7
8
9
Mechanical
1 | forums |  | Dome |  | $490.00 | 1 | $490.00
2 | forums |  | Outer Feet |  | $350.00 | 1 | $350.00
3 | forums |  | Center Feet |  | $150.00 | 1 | $150.00
4 | TBD | TBD | bonding material | mounting things in dome | $7.00 | 5 | $35.00
5 | TBD | TBD | brass board material | nice wood | $16.00 | 1 | $16.00
6 | grainger? | TBD | Small parts (nuts/bolts) | packages 100 screws and 100 nuts various sizes | $10.00 | 10 | $100.00
7 | TBD | TBD | paint | TBD | $10.00 | 10 | $100.00
8 | TBD | TBD | Battery boxes | cover motors on feet … assume set | $100.00 | 1 | $100.00
9 | TBD | TBD | Acitone | 3d printing | $12.00 | 1 | $12.00
10 | TBD | TBD | Metalic ABS | 3d printing | $50.00 | 1 | $50.00
11 | TBD | TBD | Resin | 3d printing | $175.00 | 1 | $175.00
12 |  |  |  |  |  |  | $0.00
13 |  |  |  |  |  |  | $0.00
14
15
 | Sum |  |  |  |  |  | $3411.10
 | Margin |  |  |  |  |  | $682.22
 | Total |  |  |  |  |  | $4093.32

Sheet: FundingBudget
No. | Part | Unit Price | Quantity | Sum
1 | Ultrasonic Sensor (5 pieces) | $9.99 | 2 | $19.98
2 | IR Sensor | $6.99 | 8 | $55.92
3 | Orientation Sensor | $14.95 | 3 | $44.85
4 | Raspberry Pi Camera | $19.95 | 2 | $39.90
5 | Servo | $5.95 | 14 | $83.30
6 | Speaker | $1.95 | 3 | $5.85
7 | 8x8 LED Matrix with Backpack | $15.95 | 16 | $255.20
8 | LED Flashlight (5 pieces) | $7.95 | 2 | $15.90 | Electronics Total
9 | LED Driver | $7.95 | 3 | $23.85 | $1055.89
10 | Simple Motor Controller | $33.95 | 2 | $67.90
11 | Sabertooth Motor Controller | $124.99 | 2 | $249.98
12 | PWM-servo Controller | $14.95 | 2 | $29.90
13 | Voltage Regulator (12V to 3.3V) | $8.95 | 3 | $26.85
14 | Voltage Regulator (12V to 5.0V) | $27.95 | 3 | $83.85
15 | LED Fan | $14.99 | 1 | $14.99
16 | WiFi Adapter | $8.95 | 1 | $8.95
17 | MicroSD Card | $10.41 | 2 | $20.82
18 | 3x4 Keypad | $3.95 | 2 | $7.90
19 | Dome | $490.00 | 1 | $490.00
20 | Outer Feet | $350.00 | 1 | $350.00
21 | Center Feet | $150.00 | 1 | $150.00 | Electrical & Mechanical Total
22 | Silver ABS Filament | $50.00 | 1 | $50.00 | $1319.00
23 | Motorcycle Battery | $210.00 | 1 | $210.00
24 | Smart Charging Cable | $57.00 | 1 | $57.00
25 | Entension Cord | $12.00 | 1 | $12.00
Total System Cost |  |  |  | $2374.89
Total Alloted for Project |  |  |  | $3000.00
Slack Budget |  |  |  | $625.11

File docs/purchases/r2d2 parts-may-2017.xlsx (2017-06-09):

No. | Source | Part Number | Item | Price | Quantity | Sum | Link
1 | Adafruit | 1052 | Adafruit Small 1.2" 8x8 LED Matrix w/I2C Backpack - Blue | 11.95 | 7 | 83.65 | https://www.adafruit.com/product/1052
2 | Adafruit | 902 | Adafruit Bicolor LED Square Pixel Matrix with I2C Backpack | 15.95 | 2 | 31.9 | https://www.adafruit.com/product/902
3 | Adafruit | 3006 | Adafruit I2S 3W Class D Amplifier Breakout - MAX98357A | 5.95 | 2 | 11.9 | https://www.adafruit.com/product/3006
4 | Adafruit | 815 | Adafruit 16-Channel 12-bit PWM/Servo Driver - I2C interface - PCA9685 | 14.95 | 2 | 29.9 | https://www.adafruit.com/product/815
5 | Adafruit | 3463 | Adafruit Precision NXP 9-DOF Breakout Board - FXOS8700 + FXAS21002 | 14.95 | 2 | 29.9 | https://www.adafruit.com/product/3463
6 | Adafruit | 3367 | Mini USB Microphone | 5.95 | 2 | 11.9 | https://www.adafruit.com/product/3367
7 | Adafruit | 3421 | Adafruit I2S MEMS Microphone Breakout - SPH0645LM4H | 6.95 | 4 | 27.8 | https://www.adafruit.com/product/3421
8 | Adafruit | 1196 | Slip Ring with Flange - 22mm diameter, 12 wires, max 240V @ 2A | 19.95 | 1 | 19.95 | https://www.adafruit.com/product/1196
 | Sum |  |  |  |  | 246.9

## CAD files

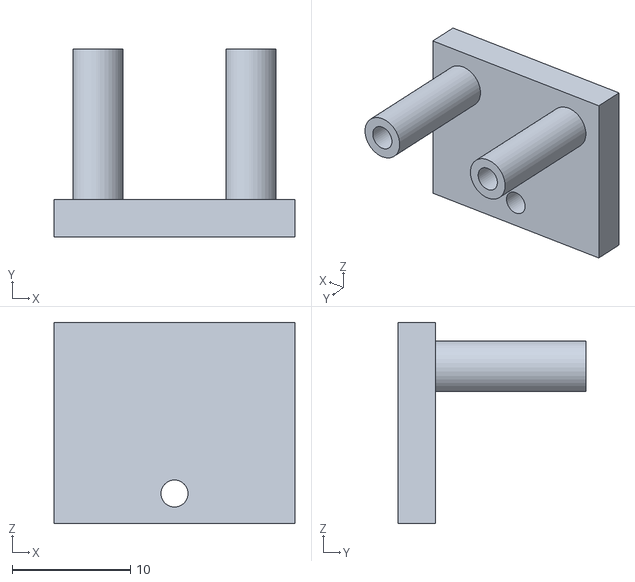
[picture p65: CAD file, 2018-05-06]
final_design/mechanical/stl/Brass Board Current Sensor Mount.STL
20.4 x 15.9 x 17.0

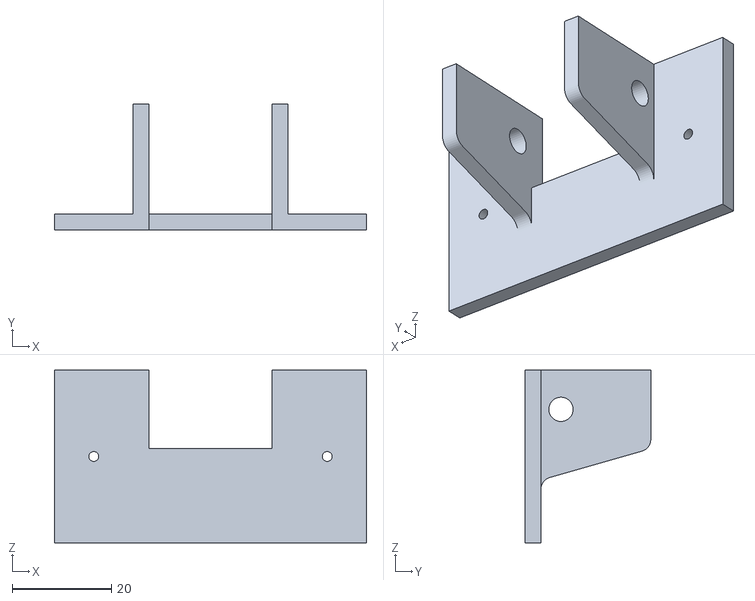
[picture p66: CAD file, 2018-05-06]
final_design/mechanical/stl/Brass Board Fan Mount.STL
63.0 x 25.4 x 34.9

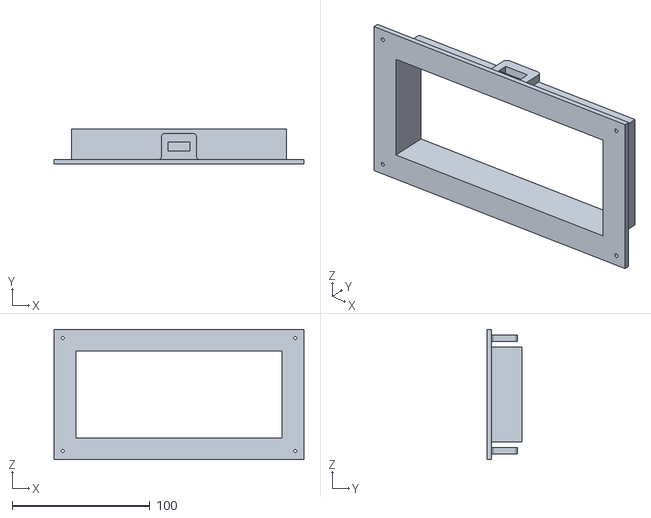
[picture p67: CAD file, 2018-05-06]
final_design/mechanical/stl/Brass Board Battery Mount.STL
181.6 x 25.4 x 94.7

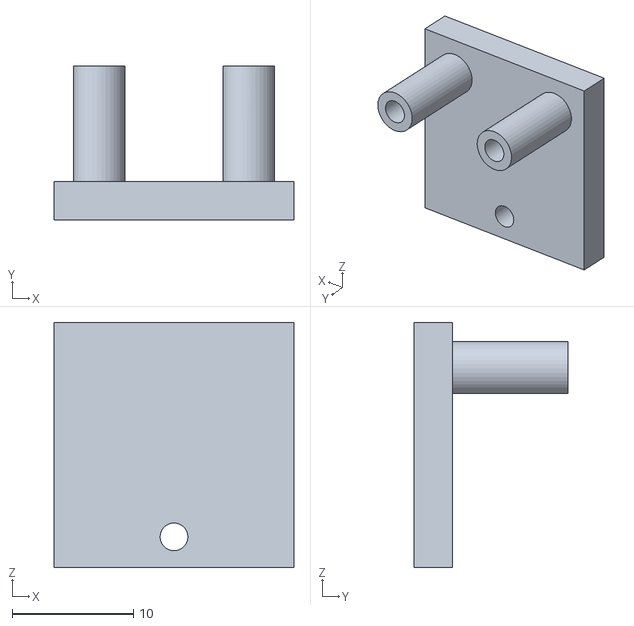
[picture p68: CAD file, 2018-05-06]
final_design/mechanical/stl/Brass Board Amplifier Mount.STL
19.8 x 12.7 x 20.2

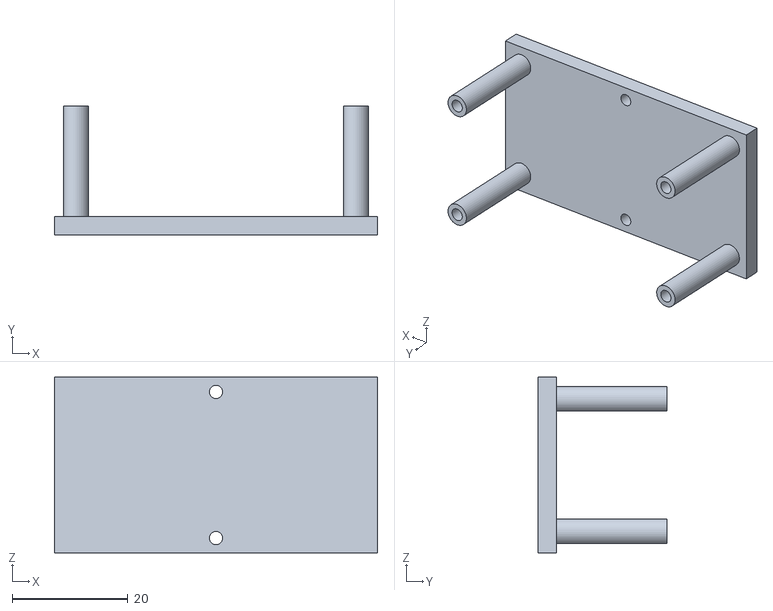
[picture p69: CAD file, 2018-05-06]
final_design/mechanical/stl/Brass Board Polulu Motor Controller.STL
55.7 x 22.2 x 30.3

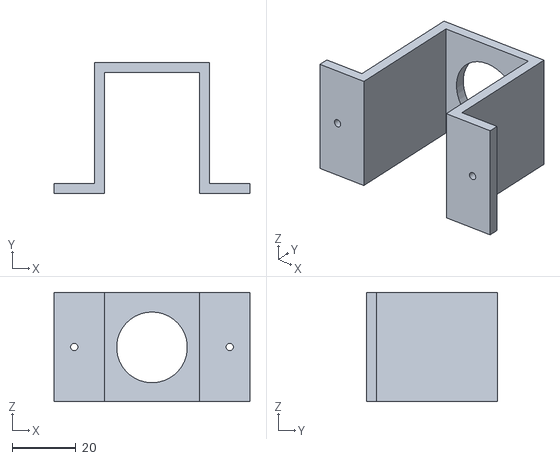
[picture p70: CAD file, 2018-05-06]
final_design/mechanical/stl/Brass Board EMS Switch Mount.STL
61.6 x 41.2 x 34.3

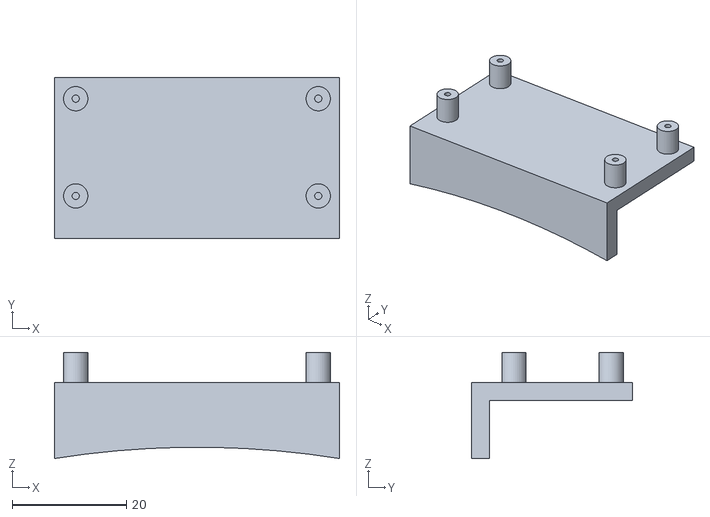
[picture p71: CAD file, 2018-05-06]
final_design/mechanical/stl/Body Ultrasonic Mount.STL
50.0 x 28.2 x 18.6

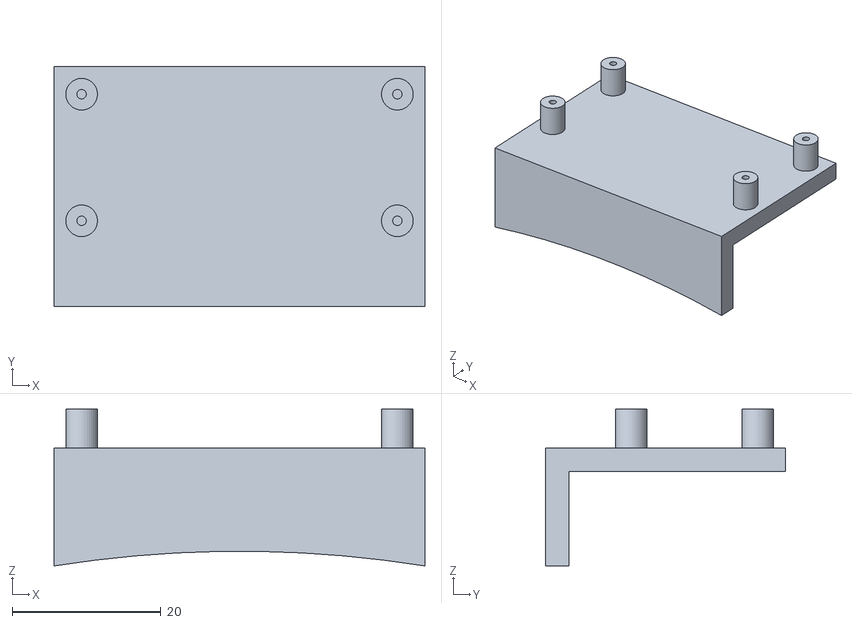
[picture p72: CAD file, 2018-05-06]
final_design/mechanical/stl/Body Ultrasonic Mount (front).STL
50.0 x 32.3 x 21.1

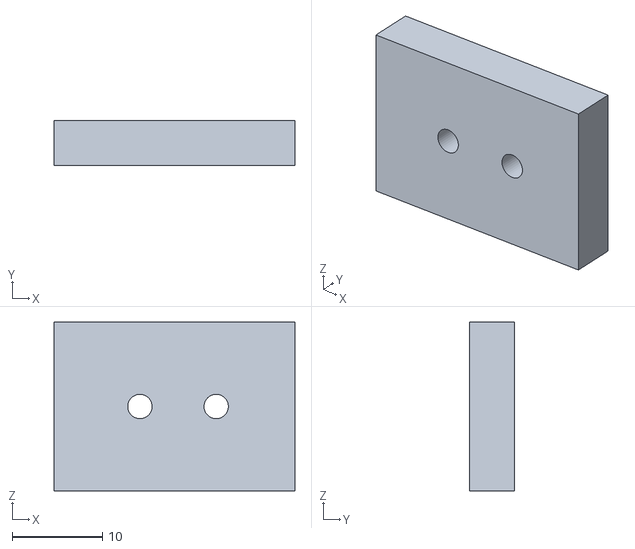
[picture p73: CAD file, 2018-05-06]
final_design/mechanical/stl/Dome Motor Mount Top.STL
26.7 x 5.00 x 18.7

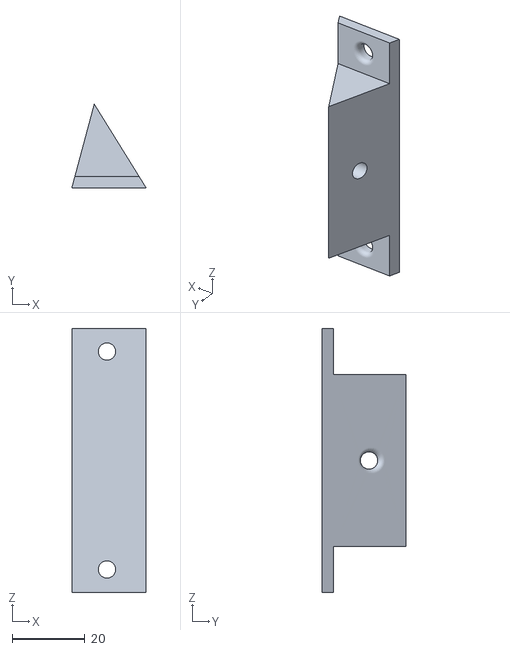
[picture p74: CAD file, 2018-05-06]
final_design/mechanical/stl/Front Foot Rotation Stopper.STL
20.5 x 23.1 x 72.7

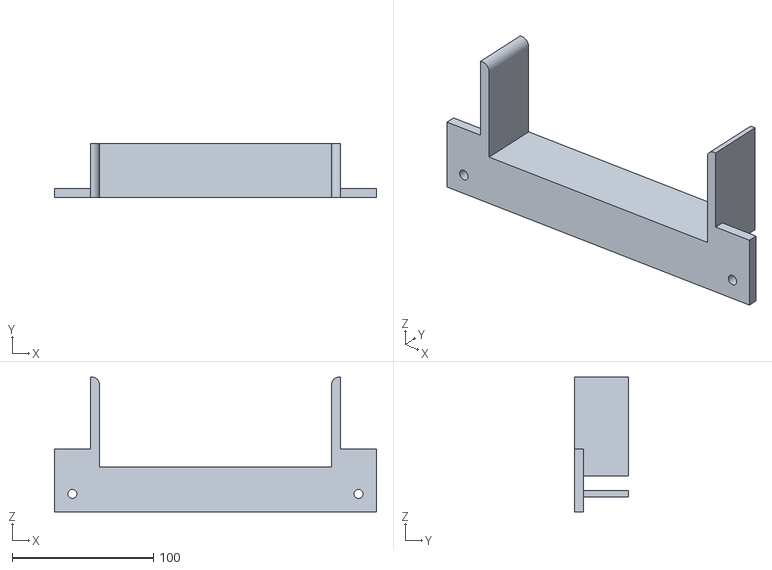
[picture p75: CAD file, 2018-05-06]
final_design/mechanical/stl/Body Battery Mount.STL
227.7 x 38.1 x 95.2

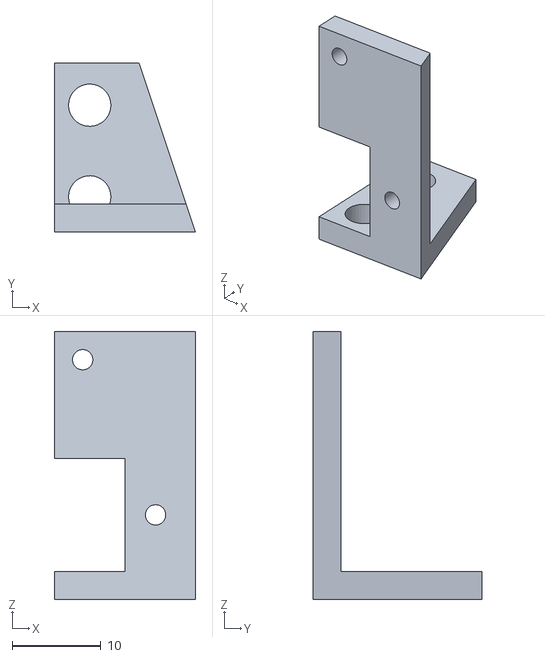
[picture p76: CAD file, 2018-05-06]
final_design/mechanical/stl/Brass Board Servo Mount right.STL
15.9 x 19.1 x 30.2

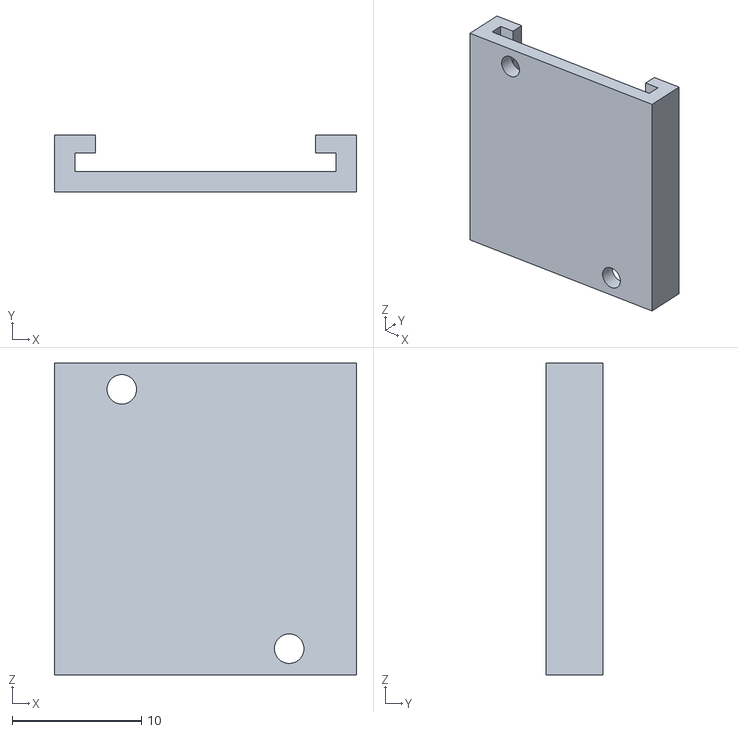
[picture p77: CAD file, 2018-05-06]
final_design/mechanical/stl/Brass Board LED Flashlight Mount.STL
23.4 x 4.43 x 24.1

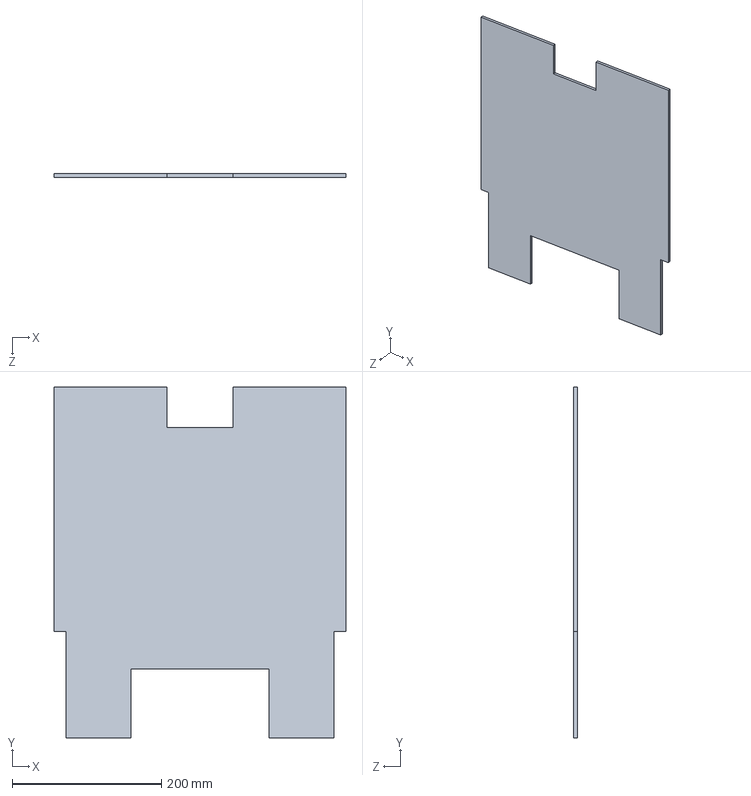
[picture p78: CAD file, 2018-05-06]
final_design/mechanical/stl/Control Panel Dimensions.SLDPRT
390.5 x 469.9 x 4.76 mm

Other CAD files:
final_design/mechanical/stl/Brass Board Push Button Mount.STL
final_design/mechanical/stl/Back Foot Housing (LEFT1).STL
final_design/mechanical/stl/Front Wheel Housing.STL
final_design/mechanical/stl/Front Foot Slot Inserts.STL
final_design/mechanical/stl/Back Feet Battery Box 1.STL
final_design/mechanical/stl/Back Feet Battery Box 2.STL
final_design/mechanical/stl/Back Foot Housing (LEFT).STL
final_design/mechanical/stl/Back Foot Housing (LEFT2).STL
final_design/mechanical/stl/Back Foot Housing (RIGHT1).STL
final_design/mechanical/stl/Back Foot Housing (RIGHT2).STL
final_design/mechanical/stl/Body Flashlight Driver.STL
final_design/mechanical/stl/Body LED PCB Mount.STL
final_design/mechanical/stl/Body PWM-Servo Controller Mount.STL
final_design/mechanical/stl/Body Speaker Cover.STL
final_design/mechanical/stl/Brass Board 3.3V Voltage Regulator Mount.STL
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

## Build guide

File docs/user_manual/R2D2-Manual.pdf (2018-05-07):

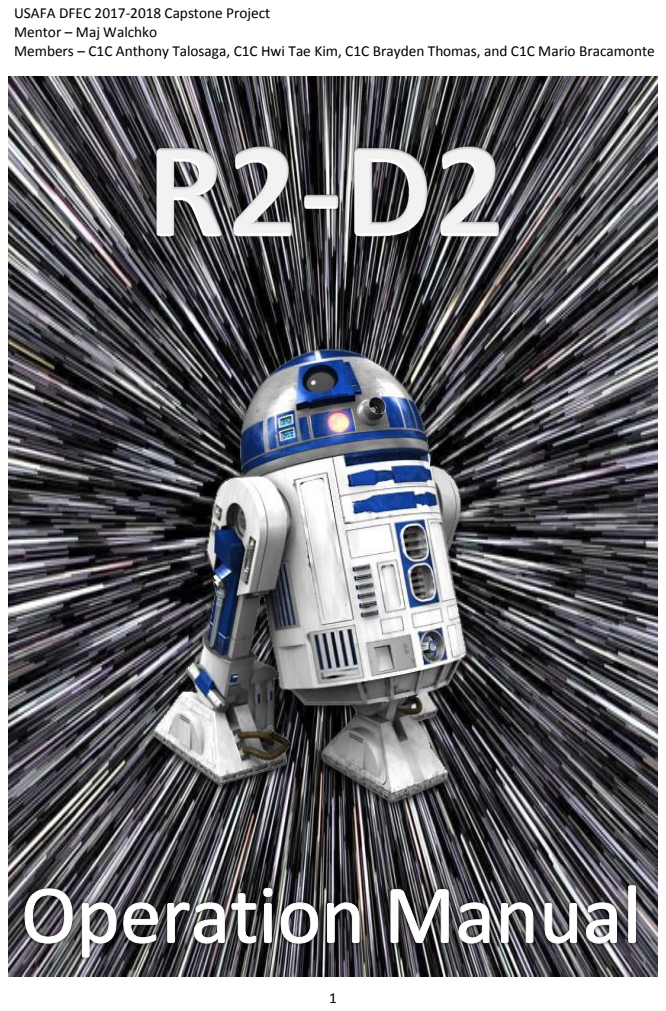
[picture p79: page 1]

USAFA DFEC 2017-2018 Capstone Project
Mentor – Maj Walchko
Members – C1C Anthony Talosaga, C1C Hwi Tae Kim, C1C Brayden Thomas, and C1C Mario Bracamonte

# Table of Contents

Safety Measures | Page 3
R2-D2 Terminologies | Page 4-6
Operation Procedures | Page 7-8
Keypad Controls | Page 9
PS4 Controls | Page 10
Battery and External Power | Page 11-12
Troubleshooting | Page 13-15

## Safety Measures

- Press EMS switch to shut down all motors during an emergency situation
- Have a fire extinguisher in close proximity for fire hazards
- Do NOT connect the charging plug and external plug at the same time!
- Ensure battery is at a minimum of 20% to prevent discharge malfunctions
- Make sure to unscrew one of the battery terminal if battery is not used
- Dispose old batteries properly
- Current R2-D2 wheels (as of May 2018) are only compatible to drive inside Fairchild hallways
- Avoid nearby stairways at all times
- Avoid driving R2-D2 at full speed to prevent collision with nearby people
- Seek professional assistance if the troubleshooting methods in this manual does not fix any software, electrical, or mechanical problems

## R2-D2 Terminologies

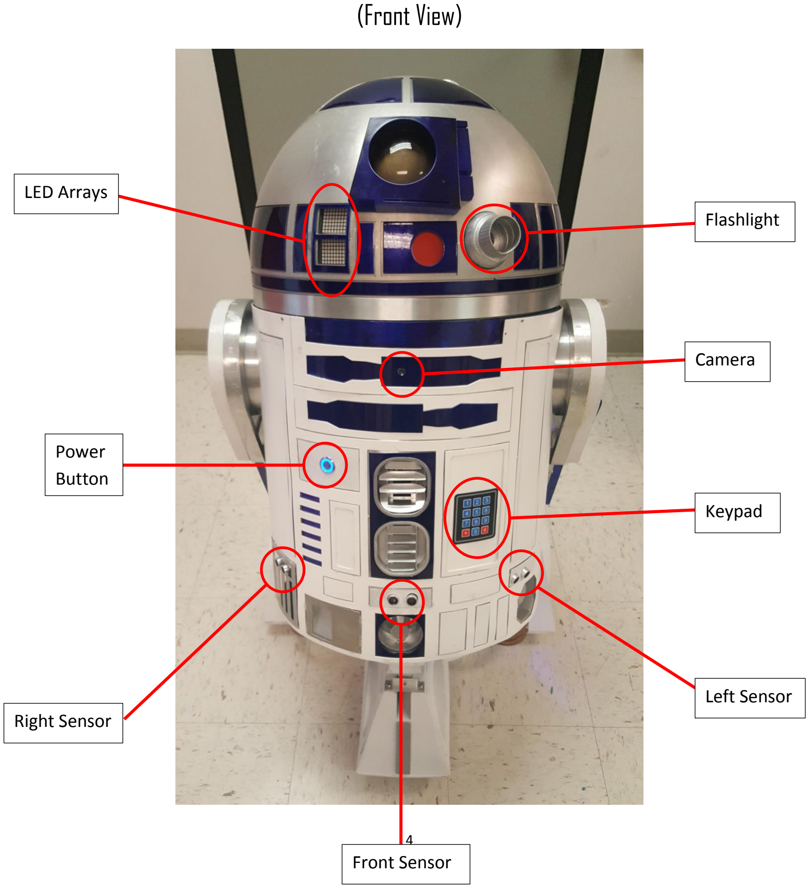
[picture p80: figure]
(Front View); LED Arrays; Right Sensor; Power Button; Front Sensor; Left Sensor; Keypad; Camera; Flashlight
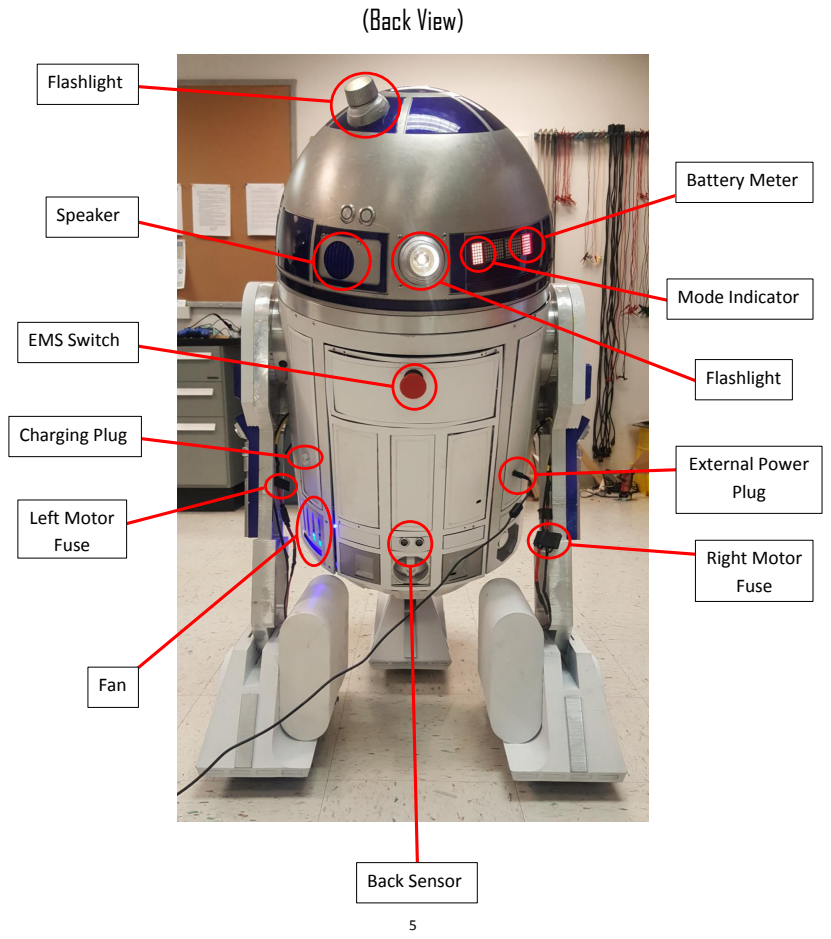
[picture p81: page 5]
(BackView); Flashlight; Speaker; EMS Switch; Left Motor Fuse; Fan; Back Sensor; Right Motor Fuse; Mode Indicator; Battery Meter; Charging Plug; External Power Plug

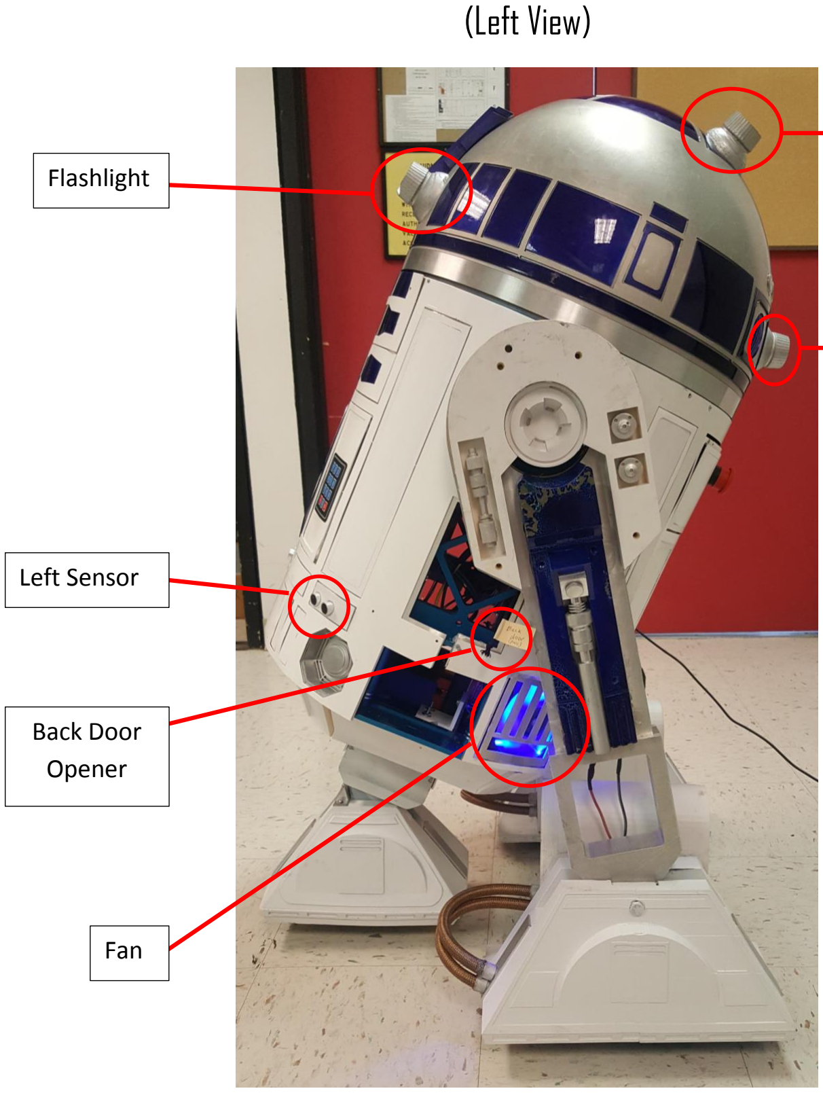
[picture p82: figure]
(Left View); Back Door Opener; Fan; Left Sensor; Flashlight

Flashlight

Flashlight

## Operation Procedures

1) - Press the power button to turn ON power (if using battery)
- Plug in external power plug (if using external power)
2) - Wait for “Window XP” startup sound to play (signals startup success)
- If power fails, turn power button OFF/ON or unplug/plug external power
3) - Afterwards, connect PS4 controller by pressing and holding the “share” and “PlayStation” button together until the blue light starts blinking.
- Connection is successful when the blue light stops blinking and turns dark blue.
- Connection is unsuccessful when the blue light stops blinking and/or turns light blue.
- If connection is unsuccessful, try re-connecting the PS4 controller or restart the entire system by pressing the “Reboot” button on the keypad.

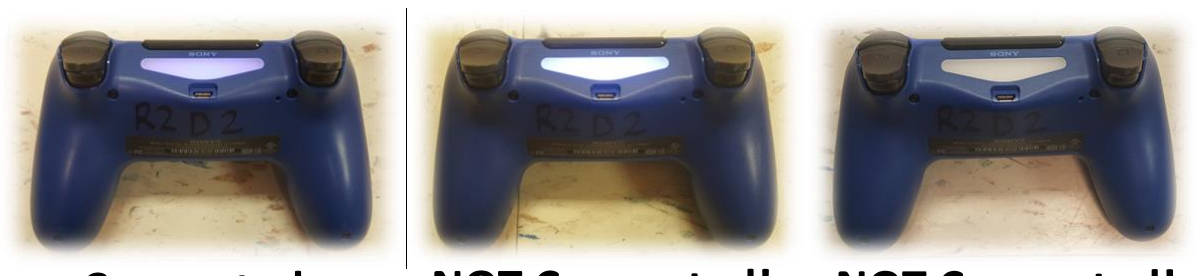
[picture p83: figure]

4) - Press number 1 on keypad to activate “Standby” mode or safe mode
Connected | NOT Connected! | NOT Connected!

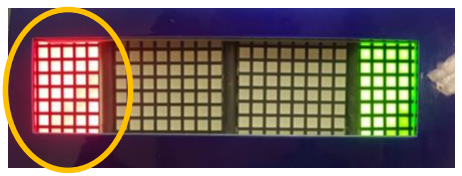
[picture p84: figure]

“Red” Color Indicator

5) - Press number 2 on keypad to activate “Static display” mode

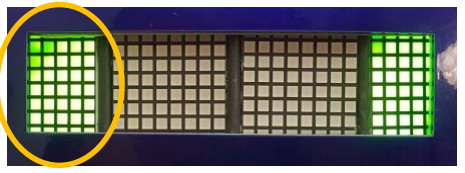
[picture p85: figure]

6) - Press number 3 on keypad to activate “Remote” mode -You can only use PS4 controller during “Remote” mode

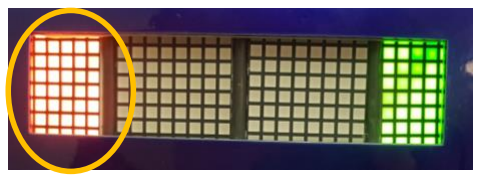
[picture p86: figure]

7) - Press number 4, 5, or 6 on keypad to activate “Happy”, “Chill” , or

“Angry”
emotions
8) - Press the star key (*) to reboot/restart the system
9) - Press the pound key (#) to shut down the system
- The “Window XP” shutdown sound will play immediately
- After 15 seconds, press the power button to turn OFF the power

IMPORTANT → Press EMS to shut down all motors during an emergency situation

Go to this link for a quick Demo → https://youtu.be/QTvInzK1VoA

“Green” Color Indicator

“Orange” Color Indicator

## Keypad Controls

1) Mode selection buttons:
- Press number 1 for “standby” or safe mode
- Press number 2 for “static display” mode
- Press number 3 for “remote” mode
2) Emotion selection buttons:
- Press number 4 for “Happy”
- Press number 5 for “Chill”
- Press number 6 for “Angry”
3) Software power buttons:
- Press (*) for “restart/reboot”
- Press (#) for

“shutdown

Mode Buttons

Emotion Buttons

Reboot/Restart

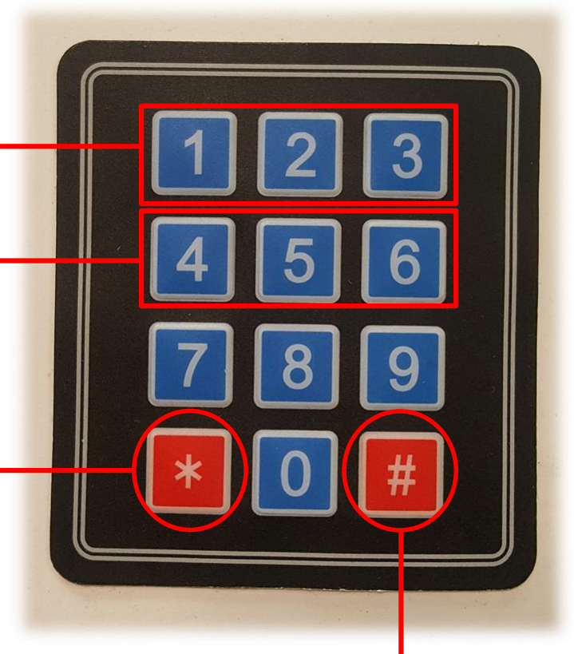
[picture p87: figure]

Shutdown

## PS4 Controls

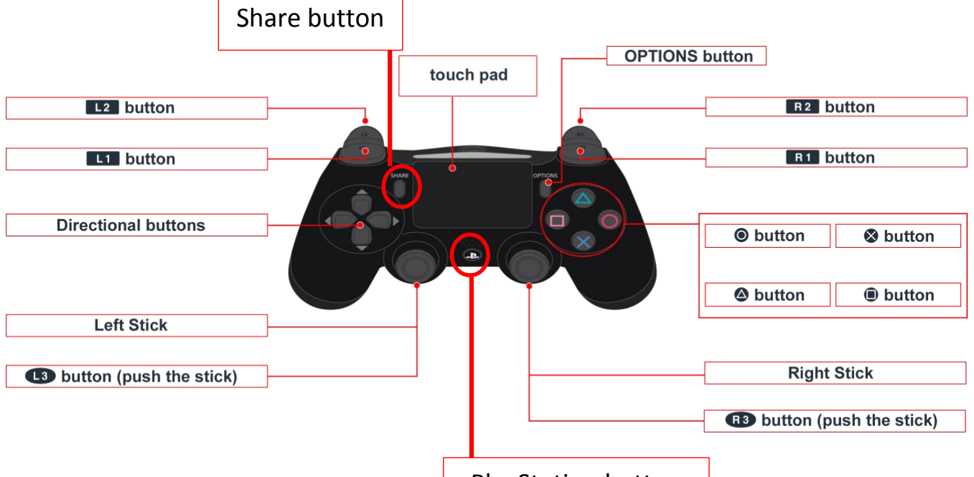
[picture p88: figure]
Share button

Triangle – Turn ON flashlights Circle – Turn OFF flashlights Square – R2-D2 talking
X – Random LED array patterns Up button – “Happy” emotion Left button – “Chill” emotion
Right button – “Angry” emotion
Left joystick (push left) – Turn left
Left joystick (push right) – Turn right Right joystick (push up) – Move backward Right joystick (push down) – Move forward R1 button – Turn dome clockwise
L1 button – Turn dome counter clockwise
R2 button – Close dome panels
L2 button – Open dome panels
Share + PlayStation buttons – Connect PS4 controller to R2-D2

PlayStation button

## Battery and External Power

Battery Replacement:

1) Ensure power button is OFF
2) Open and close back door using back door opener (strap) on the left side
3) Unscrew battery terminals and disconnect battery strap
4) Remove old battery and insert new battery
a. Recommend Lithium Iron Phosphate 12V 35Ah (or higher) battery
5) Connect strap and screw in battery terminals
a. Unscrew one terminal if battery is not currently in used

External Power Plug:

- Do NOT connect the charging plug and external plug at the same time!
- Ensure one of the battery terminals is disconnected when using external power

Charging Plug:

- Do NOT connect the charging plug and external plug at the same time!
- Utilize “Battery Meter” to keep track of battery power percentage
- Ensure battery is at 20% or higher to prevent discharge malfunctions

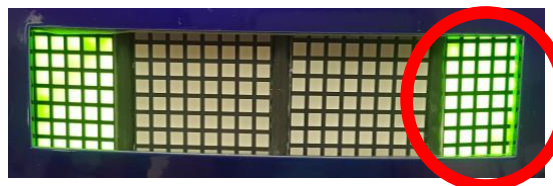
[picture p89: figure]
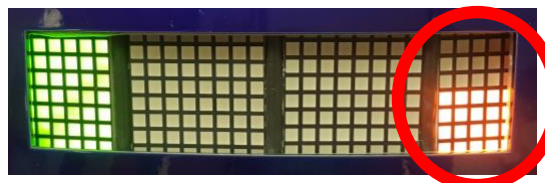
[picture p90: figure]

100% Battery | 50% Battery

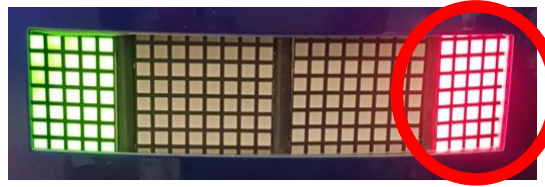
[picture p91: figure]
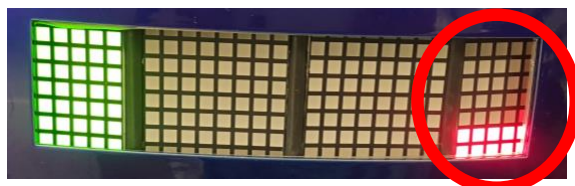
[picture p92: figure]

- Battery can be charged inside of R2-D2 by connecting the charge plug
- Battery can also be taken out and charged using the external charge plug
- A fully charged battery (10% to 100%) takes at least 3 hours
25% Battery | 0% Battery

## Troubleshooting

Software:

- If “Window XP” startup sound does not play 30 secs after startup, turn power button OFF/ON or unplug/plug external power plug
- If keypad does not work after a successful startup, turn power button OFF/ON or unplug/plug external power plug
- If all other electronics, except the keypad, does not work after a successful startup, press the star key (*) to reboot – Do NOT turn OFF power button
- If PS4 controller does not connect after 3 disconnecting/reconnecting tries, press the star key (*) to reboot – Do NOT turn OFF power button
- If any electronic glitches (especially the sensors, speaker, and keypad)…
a. Press number 1 on keypad twice for “Standby” mode
b. Press the star key (*) to reboot
c. Otherwise, turn power button OFF/ON for hard reset
- If a motor glitch occurs, press EMS switch for emergency situation before turning power OFF/ON or unplug/plug external power plug
- Seek professional assistance regarding code modification on Raspberry Pi and Arduino (user can connect HDMI and USB cables by accessing the control panel through the back door) – Warning: code modification can break the original R2-D2 program code

Electrical:

- Consider troubleshooting “software” first before troubleshooting any electrical issues
- Ensure power button is turned OFF, battery terminals disconnected, external power plug disconnected, and charging plug disconnected before troubleshooting
- Consider wearing safety glasses to prevent any eye injury
- If any electrical components does not work after a successful startup, open the back door to check any wire disconnection on the control panel and dome area
- If the dome motor does not work…
a. Check that EMS switch is OFF
b. Otherwise, check for mechanical problems
- If one of the leg motors does not work…
a. Check to make sure EMS switch is OFF
b. Check if the fuse is burnt or not – If so, change fuse (20 A min)
c. Otherwise, check for mechanical problems
- Seek professional assistance for more serious electrical issues

Mechanical:

- Ensure power button is turned OFF, battery terminals disconnected, external power plug disconnected, and charging plug disconnected before troubleshooting
- Consider troubleshooting “electrical” issues first before troubleshooting for mechanical problems

- If dome head does not spin, check to make sure that dome motor axel is not loose – if so, consider 3D printing another axel or getting another metal axel
- If a leg wheel does not spin, check to make sure the motor axel is not loose – if so, tighten the axel or consider getting a new axel gear if broken
- If squeaky sounds becomes noticeable, put some oil or WD-40 on the wheel chain
- If any skin panel falls off, recommend reattaching skin with epoxy
- Seek professional assistance for any other mechanical problems

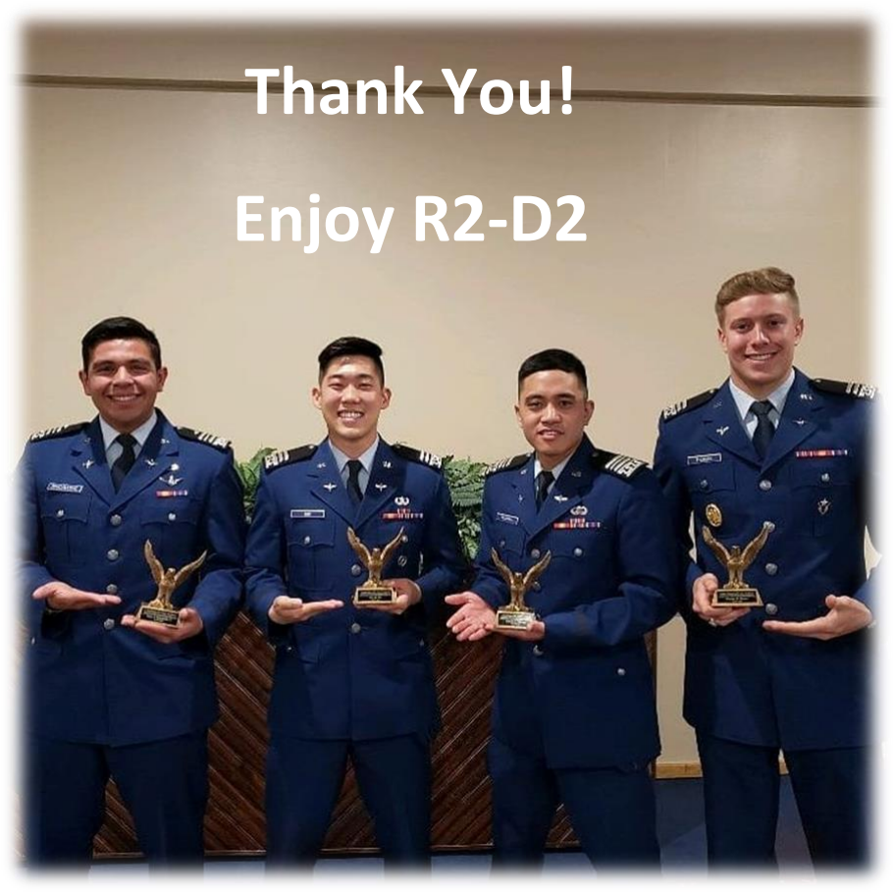
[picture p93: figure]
Thank You!; Enjoy R2-D2

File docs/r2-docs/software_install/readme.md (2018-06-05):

---
title: Install Software for ECE387
author: Kevin J. Walchko
header-includes:
    - \usepackage{fancyhdr}
    - \pagestyle{fancy}
    - \fancyhead[CO,CE]{ECE 387}
    - \fancyfoot[CO,CE]{\thepage}
    - \fancyfoot[LE,RO]{Robots are cool!}
---

# Install

To get this to work, you need the following software installed on your laptop:

- `git-bash` to get use to the command line we will be using on our linux robots
- `python` which will be our primary programming language
- OpenCV 3.4.x for computer vision
- Jupyter notebooks, most of the class material is written in this and you will need it to turn some homeworks and labs

**WARNING:** 10CS loves to do a horrible job! Some people have issues with using the `pip` command
and get an error about SSL certificates. That is the EDU firewall screwing with us. Please just
go somewhere (like Arnold Hall which has open wifi or McDonalds) and run the command from there.

**WARNING:** Please follow the instructions to the letter and in order. They are correct! I 
have installed all of this software following these instructions on multiple computers.

## Git-Bash

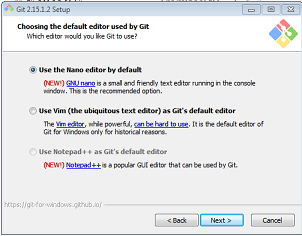
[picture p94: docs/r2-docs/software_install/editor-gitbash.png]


1. Grab the git-bash package from [git-scm.com](https://git-scm.com/download/win)
    1. Take the default options, but there is a new one, see below:
    1. Something like the second window now asks if you want to install the nano text editor. I like
    nano, it is a very simple editor. Otherwise your default is vim, which is insanely complex
    and I personnally dislike.
1. Now to open a bash window, you can double click on the git-bash icon on your desktop or from the start menu: All Programs -> Git -> Git Bash

Also to make your life a little easier, use this `.bash_profile` (*note:* there
is a `.` on the front of the file name to indicate it is hidden). Just place this
in a simple text file and leave it in your home directory `C:/Users/<your name>`, my home folder, 
for example, is: `C:/Users/Kevin.Walchko`:

```bash
# start .bash_profile -------------------------
export PATH=/c/Python27:/c/Python27/Scripts:$PATH
alias python='winpty /c/Python27/python.exe'
alias pip='python -m pip'
alias ll='ls -lh'
alias ls='ls -Fh --color=auto --show-control-chars'

USR="\[\033[01;32m\]"
HOST="\[\033[01;35m\]"
DIR="\[\033[01;34m\]"
END="\[\033[0m\]"

export PS1="$USR\u@$HOST\h $DIR\W$END \$ "

# for some stupid reason, bash starts at root level
cd ~

# end .bash_profile ---------------------------
```

If there is already a `.bash_profile` there, then overwrite it with this one.

## Python

### Microsoft Compiler for Python 2.7

In order to build some of the python packages we need, you have to have a compiler
installed. For linux/unix, this isn't an issue. For Windoze, we need to get and
install one.

1. Download the [https://www.microsoft.com/en-us/download/details.aspx?id=44266](https://www.microsoft.com/en-us/download/details.aspx?id=44266)
1. Once you have it, double click and install it

### Install Python

**YOU MUST USE PYTHON 2.7**

1. Grab the python package from [https://www.python.org/downloads/windows/](https://www.python.org/downloads/windows/)
1. You should have something like `python-2.7.14.amd64.msi` which is the x86-64 MSI
installer, run that and install the software to your C: drive. Just take all of the default
options. You should end up with C:/Python27 on your hard drive. If not, you did something
wrong. Uninstall and try again.
1. Open a bash window
1. Update your software with: `pip install -U pip setuptools wheel`
1. Then install other python libraries: `pip install -U ar_markers future pysparklines pyserial the_collector numpy PyYAML nose simplejson fake-rpi build-utils`
1. Now do `pip list` and you should see each one of the above libraries installed.
Some of these will pull in other libraries too, so they maybe more than just the
above.

## OpenCV 3.4.0 (or newest)

1. Download OpenCV 3.4.x from [https://github.com/opencv/opencv/releases](https://github.com/opencv/opencv/releases). Look for a file name like `opencv-3.4.0-vc14_vc15.exe`. Obviously if the current version is `3.4.2`, the the filename will have that version number in it instead of `3.4.0` Your browser should put it in your `Downloads` folder. If it goes else where, then adjust the instructions below.
1. Go to the download location and double click on the `exe`, this will decompress it and create a `opencv` folder
1. Grab the opencv library (`cv2.pyd`) and put it into your python library
    1. from: `C:\Users\<your username>\Downloads\opencv\build\python\2.7\x64\cv2.pyd`
    1. to: `C:\Python27\Lib\site-packages`
1. Now test:
    1. open a bash window
    1. run: `python`
    1. type: `import cv2`
    1. if there are no errors ... you are good!
    1. type: `cv2.__version__` and the current version should come up ... something like 3.4.0 or whatever version you downloaded.
    1. If you have errors, you did something wrong! You have to put the library exactly where
    I told you and you have to have the python libraries (using `pip`) from the python install
    section installed. OpenCV depends on `numpy` and will crash if not installed.

If you ever need to update your system to a new version, like `3.4.4`, you can repeat this process. You *might* need to update the python library `numpy`, but that should be easily fixed with" `pip install -U numpy`. OpenCV and `numpy` are tighly coupled.

## Jupyter Notebooks

You have to have Python and GitBash installed already before you do this.

1. Open a bash window
1. Run: `pip install -U pip setuptools wheel`
1. Run: `pip install -U numpy jupyter opencvutils matplotlib jupyter_tools sympy`
1. Run `pip list` and you should see each one of these libraries installed. If not then
redo it.
1. Once that finishes installing, run: `jupyter notebook`
1. A webpage should open up. From there you can create or
   navigate to where your jupyter notebooks are stored and open them.

## [OPTIONAL] VS Studio

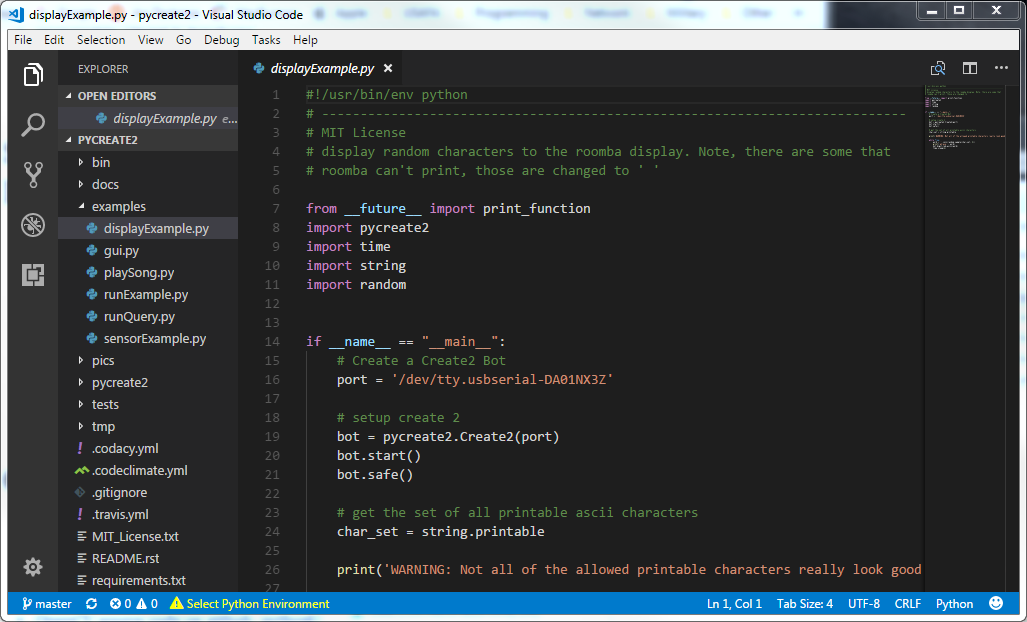
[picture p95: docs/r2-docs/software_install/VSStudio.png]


I am not a microsoft fan, but 10CS makes using my editor of choice [Atom](https://atom.io/) 
difficult to use here at USAFA. I have played around with Visual Studio Code which is **very**
similar to Atom, so I will suggest it if you need a decent python editor.

Download: https://code.visualstudio.com/?wt.mc_id=DX_841432

Just remember I haven't really done much with it yet.

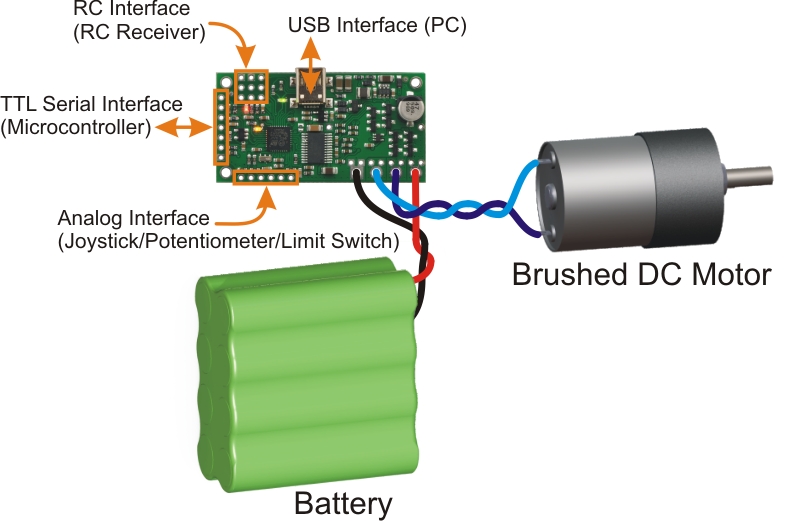
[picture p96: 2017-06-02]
docs/datasheets/pololu_SMC/smc-wiring.jpg

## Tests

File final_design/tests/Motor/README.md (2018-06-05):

#Motor Controllers

##Motor Controllers:

**Important Links**:

- Link: [Motor controller datasheet](http://support.robotis.com/en/product/auxdevice/sensor/dms_manual.htm "DMS-80 datasheet")

**Cost and Specs**:

- Cost: $14.90 per sensor

- Range: 10cm - 80cm

- Voltage level: 4.5V - 5.5V

##Preliminary design

Image Template

##References
- [Link Template](https://cdn.sparkfun.com/datasheets/Sensors/Proximity/HCSR04.pdf "Template")

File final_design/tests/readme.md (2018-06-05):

# Tests

These are a bunch of individual test scripts to exercise various parts of R2

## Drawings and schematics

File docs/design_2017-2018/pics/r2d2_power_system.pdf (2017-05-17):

## MOT1

## RoboteQ AX3500

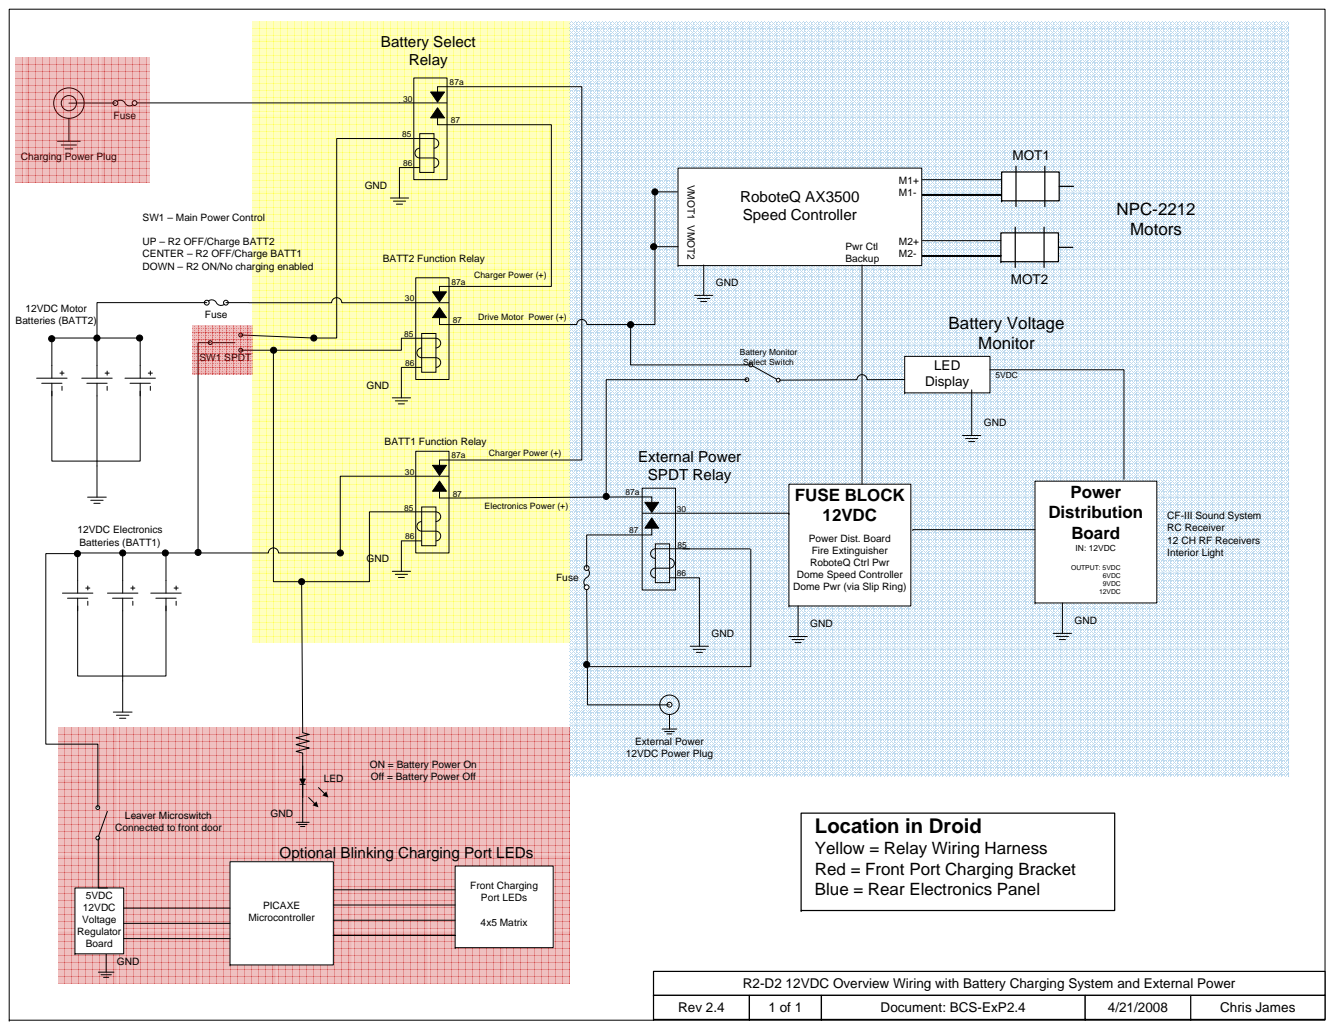
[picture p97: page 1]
Electronics Power (+); 12VDC Electronics Batteries (BATT1); External Power 12VDC Power Plug; SW1 SPDT; GND; FUSE BLOCK 12VDC; Power Distribution Board; IN: 12VDC; OUTPUT: 5VDC 6VDC 9VDC 12VDC; PICAXE Microcontroller; 5VDC 12VDC Voltage Regulator Board; Front Charging Port LEDs; 4x5 Matrix; MOT2; Speed Controller; Pwr Ctl Backup; V MOT1 VMOT2; External Power SPDT Relay; Battery Select Relay; Charger Power (+); LED; BATT1 Function Relay; BATT2 Function Relay; Rev 2.4; Document: BCS-ExP2.4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

Charging Power Plug

SW1 – Main Power Control

UP – R2 OFF/Charge BATT2
CENTER – R2 OFF/Charge BATT1
DOWN – R2 ON/No charging enabled

Drive Motor Power (+)

CF-III Sound System
RC Receiver
12 CH RF Receivers
Interior Light

Power Dist. Board
Fire Extinguisher
RoboteQ Ctrl Pwr
Dome Speed Controller
Dome Pwr (via Slip Ring)

ON = Battery Power On
Off = Battery Power Off

Leaver Microswitch
Connected to front door

Location in Droid
Yellow = Relay Wiring Harness
Red = Front Port Charging Bracket
Blue = Rear Electronics Panel

Optional Blinking Charging Port LEDs

R2-D2 12VDC Overview Wiring with Battery Charging System and External Power

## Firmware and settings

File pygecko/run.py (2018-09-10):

#!/usr/bin/env python2
# Author:
# Kevin Walchko


# Initialiation All Library Files
from __future__ import division
from __future__ import print_function

# python libraries
import time
import multiprocessing as mp
# from time import sleep
# import numpy as np
import os
# import string
import random
from subprocess import call
from subprocess import check_output
from math import sqrt

# python modules from pip for hardware drivers
# from pysabertooth import Sabertooth
# from smc import SMC
from nxp_imu import IMU
import RPi.GPIO as GPIO  # at the end, cleanup

# get drivers from library
from library import Sounds
from library import Arduino
from library import Keypad
# from library import Trigger, Axis, PS4, Joystick
from library import Servo, FlashlightPWM
from library import LEDDisplay
from library import LogicFunctionDisplay
from library import factory
from library import PWM
from library import ButtonLED
# from library import FlashlightGPIO

# States
from states.remote import remote_func
from states.standby import standby_func
from states.static import static_func

# Emotions
from states.emotions import angry, happy, confused

print("this file", __file__)
bin_path = __file__[:-7]  # assume file is /run.py

def getHostSerialNumber():
	ssn = None
	a=check_output(["cat", '/proc/cpuinfo'])
	for s in a.split('\n'):
		if s.find('Serial') > -1:
			ssn = s.split()[2]
	return ssn

ssn = getHostSerialNumber()

if ssn == '00000000f4e2702a':  # real R2D2
	arduino_port = '/dev/serial/by-id/usb-Arduino__www.arduino.cc__0042_95432313138351F00180-if00'
	# arduino_port = '/dev/ttyACM0'
	leg_motors_port = '/dev/serial/by-id/usb-Dimension_Engineering_Sabertooth_2x32_16001878D996-if01'
	dome_motor_port = '/dev/serial/by-id/usb-Pololu_Corporation_Pololu_Simple_Motor_Controller_18v7_52FF-6F06-7283-5255-5252-2467-if00'

	# real R2
	# process state indicator
	# they didn't include ... :(
	# front logic display
	# 0x70
	# 0x73
	# back
	# 0x75,0x71,0x72,0x74
	led_data = {
		'psi': None,  # process state indicator
		'fld': [      # front logic display (top, bottom)
			[0x70, 1],
			[0x73, 1]
		],
		'rld': [      # rear logic display (left to right)
			[0x75,1],
			[0x71,1],
			[0x72,1],
			[0x74,1]
		]
	}
	# original
	# servo_limits = {
	# 	0: [30, 60], # opened/closed
	# 	1: [94, 124],
	# 	2: [20, 49],
	# 	3: [30, 60],
	# 	4: [15, 45],
	# }
	servo_limits = {
		0: [30, 60], # opened/closed
		1: [94, 124],
		2: [20, 49],
		3: [30, 60],
		4: [15, 45],
	}

	rpi_pins = {

	}
elif ssn == '0000000019b26150':  # breadboard system
	arduino_port = 'loop://'
	leg_motors_port = '/dev/serial/by-id/usb-Dimension_Engineering_Sabertooth_2x32_16004F410010-if01'
	dome_motor_port = '/dev/serial/by-id/usb-Pololu_Corporation_Pololu_Simple_Motor_Controller_18v7_50FF-6D06-7085-5652-2323-2267-if00'
	led_data = {
		'psi': [0x75, 0],               # process state indicator
		'fld': [[0x70, 1], [0x73, 0]],  # front logic display (top, bottom)
		'rld': [[0x71,0], [0x72,0], [0x74,0]]    # rear logic display (left to right)
	}

	servo_limits = {
		0: [30, 60], # opened/closed
		1: [94, 124],
		2: [20, 49],
		3: [30, 60],
		4: [15, 45],
	}
else:
	print("Couldn't get Host serial number from /proc/cpuinfo ... exiting")
	print("Function return:", ssn)
	exit(1)

# Reboots R2D2
def reboot():
	# namespace.audio.sound('shutdown')
	call("sudo service r2d2 stop", shell=True)
	call("sudo service r2-webserver stop", shell=True)
	time.sleep(1)
	call("sudo reboot now", shell=True)
	time.sleep(3)
	return


# Shutdowns R2D2
def shutdown():
	# namespace.audio.sound('shutdown')
        call("sudo service r2d2 stop", shell=True)
        call("sudo service r2-webserver stop", shell=True)
	time.sleep(1)
	call("sudo shutdown", shell=True)
	time.sleep(3)
	return


def normalize(v):
	d = sqrt(v[0]**2 + v[1]**2 + v[2]**2)
	ret = (0, 0, 0,)
	if d > 0.1:
		m = 1/d
		ret = (v[0]*m, v[1]*m, v[2]*m,)
	return ret


def arduino_proc(flag, ns):
	"""
	This process talks to the arduino via serial comm. All data is pushed
	into shared memory
	"""
	ser = Arduino(arduino_port, 19200)

	while flag.is_set():
		time.sleep(0.25)

		# read battery
		# ser.write(b'2')
		# d = ser.readline()
		# d = d.replace('\r', '').replace('\n', '')
		# if d:
		# 	batt = float(d)
		# 	ns.battery = batt
		# 	print("battery", batt)
		ns.battery = ser.getBattery()

		# read ultrasound
		# ser.write(b'1')
		# ultra = []
		# for i in range(4):
		# 	d = ser.readline()
		# 	d = d.replace('\r', '').replace('\n', '')
		# 	print("us",d)
		# 	if d:
		# 		d = float(d)
		# 	else:
		# 		d = -1.0
		# 	ultra.append(d)
		# ns.ultrasounds = ultra
		ns.ultrasounds = ser.getUltraSounds()

		# print('batt', ns.battery)
		print('us', ns.ultrasounds)

def i2c_proc(flag, ns):
	"""
	Everything attached to i2c bus goes here so we don't have to do semifores.
	Also, the lcd button code is here too so it is always in sync with the
	led matricies.
	"""
	print("Starting:", mp.current_process().name)
	imu = IMU(gs=4, dps=2000, verbose=False)
	leds = LogicFunctionDisplay(led_data)
	led_update = 0

	servos = []
	servo_angles = []
	for id in servo_limits:
		s = Servo(id)
		# s.setMinMax(*servo_limits[id])  # set open(min)/closed(max) angles
		s.open = servo_limits[id][0]
		s.close = servo_limits[id][1]
		s.closeDoor()  # closed
		# servo_angles.append(sum(servo_limits[id])/2)
		servos.append(s)
		servo_angles.append(s.angle)
		time.sleep(0.01)
	# init namespace to have the same angles
	ns.servo_angles = servo_angles
	Servo.all_stop()

	b_led = ButtonLED(26,16,20)

	# test ---------------------
	# vals = [True]*3
	# b_led.setRGB(*vals)
	# time.sleep(3)
	# for i in range(3):
	# 	print(i)
	# 	vals = [True]*3
	# 	vals[i] = False
	# 	b_led.setRGB(*vals)
	# 	time.sleep(3)

	while flag.is_set():
		a, m, g = imu.get()
		ns.accels = a  # accel [x,y,z] g's
		ns.mags = m    # magnetometer [x,y,z] mT
		ns.gyros = g   # gyros [x,y,z] rads/sec

		# FIXME: real hw is at a funny oriendataion
		# a = normalize(a)
		# seems that 0.80 is pretty big tilt
		# if a[2] < 0.85:
		# 	ns.safety_kill = True
		# 	print(a)
		# 	print('<<< TILT >>>')

		# update LEDs
		# OFF    = 0
		# GREEN  = 1
		# RED    = 2
		# YELLOW = 3
		led_update += 1
		if led_update % 20 == 0:
			led_update = 0
			# print('current_state',ns.current_state)
			cs, batt = ns.current_state, ns.battery

			if cs == 1:    # standby
				csc = 2    # red
				b_led.setRGB(True, False, False)
			elif cs == 2:  # static
				csc = 3    # yellow
				b_led.setRGB(True, True, True)
			elif cs == 3:  # remote
				csc = 1    # green
				b_led.setRGB(False, True, False)

			# make something up for now
			# battc = random.randint(1,3)
			if ns.set_all_leds:
				leds.setAll(ns.set_all_leds)
			else:
				leds.setFLD(csc, 1)
				leds.setRLD()

		# update servos if the have changed
		# namespace.servo_angles: another process wants to change the angle
		# servo_angles: local copy, if no difference between the 2, do nothing
		# TODO: should these just be open/close (T/F)? why angles?
		for nsa, sa, servo in zip(ns.servo_angles, servo_angles, servos):
			if nsa == sa:
				continue
			sa = nsa
			servo.angle = sa
			time.sleep(0.1)

		if ns.servo_wave:
			ns.servo_wave = False
			leds.setAll(1)
			print('servo wave')
			for s in servos:
				s.openDoor()
				time.sleep(0.2)

			# servos[1].stop()
			time.sleep(2)
			# Servo.all_stop()
			for s in servos:
				s.closeDoor()
				time.sleep(0.2)

			# servos[1].stop()
			time.sleep(2)
			Servo.all_stop()

	b_led.setRGB(False, False, False)


def keypad_proc(flag, ns):
	"""
	This thread handles the main keypad interface and sets the global state

	Also, MIGHT, do ultrasound and battery

	Keypad (https://www.adafruit.com/product/419)
	Pi pins (BCM)
	L  connector    R
	-----------------
	11 9 10 25 13 6 5
	"""
	print("Starting:", mp.current_process().name)
	# arduinoSerialData = Arduino(arduino_port, 19200)

	# WARNING: GPIO is not thread/multiprocessor safe and these need to be
	# in the same process ... or atleast I don't know how to handle them in
	# different ones
	kp = Keypad()
	# b_led = ButtonLED(6,5,13)

	# test ---------------------
	# for i in range(3):
	# 	print(i)
	# 	vals = [False]*3
	# 	vals[i] = True
	# 	b_led.setRGB(*vals)
	# 	time.sleep(3)

	while flag.is_set():
		time.sleep(0.1)

		key = kp.getKey()
		# print("key:", key)

		# if key is not None:
		# 	print('key:', key)

		# DEBUGGING CODE -----------
		# key = random.randint(1, 3)  # debug, pick random state
		# time.sleep(5)
		# key = 2
		# print('*'*10)
		# print('* Key:', key)
		# print('*'*10)
		# ---------------------------

		# if R2 has not fallen over, then check input
		if ns.safety_kill:
			key = 1  # sommething wrong, go to standby
		else:
			if key in [1, 2, 3]:
				ns.current_state = key

			elif key in [4, 5, 6]:
				# ns.emotion = key
				if key == 4:
					c = random.choice(["900", "help me", "religion", "moon", "smell"])
					ns.wav = c
				if key == 5:
					# FIXME: make mp3
					c = random.choice(["900", "help me", "religion", "moon", "smell"])
					ns.wav = c

			elif key == 7:
				ns.servo_wave = True

			elif key == 8:
				print("<<< got turn-off key press >>>")
				ns.current_state = 0
				break

			elif key == "#":
				# FIXME: not sure the right way to do this cleanly
				print("Shutting down")
				ns.shutdown = True  # shutdown linux
				ns.current_state = 0
				break

			elif key == "*":
				print("Rebooting now")
				ns.current_state = 0
				ns.reboot = True      # reboot linux
				break


if __name__ == '__main__':
	# setup a global namespace for all processes to access shared memory
	# WANING: you cannot put any HW drivers in memory, they won't work correctly.
	# Anything in shared memory needs to be picklable (python thing)
	mgr = mp.Manager()
	namespace = mgr.Namespace()

	##############################
	# This section sets up global namespace

	# OS commands
	namespace.reboot = False
	namespace.shutdown = False

	# 0: stop
	# 1: standby
	# 2: static
	# 3: remote
	namespace.current_state = 1  # default into standy mode

	# safety, R2 has fallen over, kill all motors and signal for help!!
	namespace.safety_kill = False

	# how many detects before a person is declared found
	# OpenCV can have false posatives
	namespace.opencv_person_found = 1

	namespace.wav = None
	namespace.mp3 = None

	# 0: None
	# 1: angry
	# 2: happy
	# 3: confused
	namespace.emotion = 0

	# servo settings
	namespace.servo_angles = [0]*5  # these will get reset when servos init
	namespace.servo_wave = False

	# ultra sonic sensors for safety
	namespace.ultrasounds = [0]*4

	namespace.battery = 4.5

	namespace.set_all_leds = None

	# End namespace setup
	###################################

	###################################
	# Now setup process to talk to hardware

	# setup main run flag
	run_flag = mp.Event()
	run_flag.set()

	procs = []

	# setup keypad process
	kp = mp.Process(name='keypad_proc', target=keypad_proc, args=(run_flag, namespace,))
	kp.start()
	procs.append(kp)

	# setup i2c process
	i2c = mp.Process(name='i2c_proc', target=i2c_proc, args=(run_flag, namespace,))
	i2c.start()
	procs.append(i2c)

	ar = mp.Process(name='arduino_proc', target=arduino_proc, args=(run_flag, namespace,))
	ar.start()
	procs.append(ar)

	##################################
	# setup hardware for each state/mode function
	hw = factory(dome_motor_port, leg_motors_port, bin_path)
	# b_led = ButtonLED(6,5,13)

	# test ---------------------
	# vals = [True]*3
	# b_led.setRGB(*vals)
	# time.sleep(3)
	# for i in range(3):
	# 	print(i)
	# 	vals = [True]*3
	# 	vals[i] = False
	# 	b_led.setRGB(*vals)
	# 	time.sleep(3)

	##################################
	# Main Loop
	# The program stay here until it is sent to state = 0 and exits this loop
	try:
		while not namespace.safety_kill:
			# there was a signal to shutdown this software
			if namespace.current_state == 0:
				# b_led.setRGB(False, False, False)
				print("told to stop")
				namespace.set_all_leds =  2
				time.sleep(1)
				break
			elif namespace.current_state == 1:
				# b_led.setRGB(True, False, False) # red
				standby_func(hw, namespace)
			elif namespace.current_state == 2:
				# b_led.setRGB(True, True, True)  # it doesn't really get white, more yellow
				static_func(hw, namespace)
			elif namespace.current_state == 3:
				# b_led.setRGB(False, True, False) # green
				remote_func(hw, namespace)
			else:
				print("Invalid state, going to standby mode")
				namespace.current_state = 1
	except KeyboardInterrupt:
		print("ctl-C detected")

	# shutdown processes
	run_flag.clear()
	for process in procs:
		process.join(timeout=0.1)
		if process.is_alive():
			process.terminate()

	##################################
	# clean up remaining HW stuff
	PWM.all_stop()  # shut off all servos
	# ButtonLED.cleanup()  # cleanup the gpio library stuff
	GPIO.cleanup()  # clean up gpio library stuff

	# see if we were asked to shutdown/reboot ... if so, do it
	if namespace.reboot == True:
		reboot()
	elif namespace.shutdown == True:
		shutdown()

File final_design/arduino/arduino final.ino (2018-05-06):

//Ultrasonic 1 Initialization
int trigPin = 2;
int echoPin = 3;

//Ultrasonic 2 Initialization
int trigPin2 = 4;   
int echoPin2 = 5;

//Ultrasonic 3 Initialization
int trigPin3 = 6;
int echoPin3 = 7;

//Ultrasonic 4 Initialization
int trigPin4 = 8;
int echoPin4 = 9;

//Variable Initialization
long duration, cm, inches;
long duration2, cm2, inches2;
long duration3, cm3, inches3;
long duration4, cm4, inches4;

//Battery Reading Ports Initialization
int analogPin = A3;     // potentiometer wiper (middle terminal) connected to analog pin 3
int val = 0;           // variable to store the value read

void setup() {
  Serial.begin(19200); // start the serial port

  //Ultrasonic 1 IO
  pinMode(trigPin, OUTPUT);
  pinMode(echoPin, INPUT);
  
  //Ultrasonic 2 IO
  pinMode(trigPin2, OUTPUT);
  pinMode(echoPin2, INPUT);
  
  //Ultrasonic 3 IO
  pinMode(trigPin3, OUTPUT);
  pinMode(echoPin3, INPUT);
  
  //Ultrasonic 4 IO
  pinMode(trigPin4, OUTPUT);
  pinMode(echoPin4, INPUT);
}

void loop() {
if (Serial.available()){
      int d = Serial.read()-'0';
      if ( d == 2 )
      {
      // Read Battery and LED
      val = analogRead(analogPin);     // read the input pin
      float voltage = val * (5.0 / 1023.0);
      Serial.println(voltage);      
      }
      
      if ( d == 1 )
      {
      // Ultrasonic Sensor 1
      // The sensor is triggered by a HIGH pulse of 10 or more microseconds.
      // Give a short LOW pulse beforehand to ensure a clean HIGH pulse:
      digitalWrite(trigPin, LOW);
      delayMicroseconds(5);
      digitalWrite(trigPin, HIGH);
      delayMicroseconds(10);
      digitalWrite(trigPin, LOW);
 
      // Read the signal from the sensor: a HIGH pulse whose
      // duration is the time (in microseconds) from the sending
      // of the ping to the reception of its echo off of an object.
      pinMode(echoPin, INPUT);
      duration = pulseIn(echoPin, HIGH);
 
      // convert the time into a distance
      cm = (duration/2) / 29.1;
      inches = (duration/2) / 74; 
  
      // The sensor is triggered by a HIGH pulse of 10 or more microseconds.
      // Give a short LOW pulse beforehand to ensure a clean HIGH pulse:
      digitalWrite(trigPin2, LOW);
      delayMicroseconds(5);
      digitalWrite(trigPin2, HIGH);
      delayMicroseconds(10);
      digitalWrite(trigPin2, LOW);
 
      // Read the signal from the sensor: a HIGH pulse whose
      // duration is the time (in microseconds) from the sending
      // of the ping to the reception of its echo off of an object.
      pinMode(echoPin2, INPUT);
      duration2 = pulseIn(echoPin2, HIGH);
     
      // convert the time into a distance
      cm2 = (duration2/2) / 29.1;
      inches2 = (duration2/2) / 74; 
  
      // The sensor is triggered by a HIGH pulse of 10 or more microseconds.
      // Give a short LOW pulse beforehand to ensure a clean HIGH pulse:
      digitalWrite(trigPin3, LOW);
      delayMicroseconds(5);
      digitalWrite(trigPin3, HIGH);
      delayMicroseconds(10);
      digitalWrite(trigPin3, LOW);
 
      // Read the signal from the sensor: a HIGH pulse whose
      // duration is the time (in microseconds) from the sending
      // of the ping to the reception of its echo off of an object.
      pinMode(echoPin3, INPUT);
      duration3 = pulseIn(echoPin3, HIGH);
     
      // convert the time into a distance
      cm3 = (duration3/2) / 29.1;
      inches3 = (duration3/2) / 74; 
      
      // The sensor is triggered by a HIGH pulse of 10 or more microseconds.
      // Give a short LOW pulse beforehand to ensure a clean HIGH pulse:
      digitalWrite(trigPin4, LOW);
      delayMicroseconds(5);
      digitalWrite(trigPin4, HIGH);
      delayMicroseconds(10);
      digitalWrite(trigPin4, LOW);
 
      // Read the signal from the sensor: a HIGH pulse whose
      // duration is the time (in microseconds) from the sending
      // of the ping to the reception of its echo off of an object.
      pinMode(echoPin4, INPUT);
      duration4 = pulseIn(echoPin4, HIGH);
     
      // convert the time into a distance
      cm4 = (duration4/2) / 29.1;
      inches4 = (duration4/2) / 74; 

      Serial.println(cm);
      Serial.println(cm2);
      Serial.println(cm3);
      Serial.println(cm4);
      }
  }
}

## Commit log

2016-04-08 Backup python files after first Rpi broke
    [autoBasic.py, followWall.py, interruptPrac.py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]
2016-10-19 Sonar.py created online with Bitbucket
2016-11-15 Thread_testing.py created online with Bitbucket
2016-11-15 wireless.py created online with Bitbucket
2016-11-15 wirelessV2.py created online with Bitbucket
2016-11-15 wirelessV3.py created online with Bitbucket
2016-11-15 wireless_notes created online with Bitbucket
2016-12-14 Second Arduino code for Microview Sys.
2017-05-05 autonomous motor code
2017-06-04 leds working
2018-05-06 All 3D Print Design Files
    [Back Feet Battery Box 1.STL, Back Feet Battery Box 2.STL, Back Foot Housing (LEFT).STL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]
2018-06-05 parts list
    [Parts-missing.xlsx, R2-parts .xlsx, r2d2-parts-13-Feb-18-v2.xlsx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]
2018-09-09 updates 9 sept 2018 :bento:
    [arduino_test.py, run.py, static.py]
